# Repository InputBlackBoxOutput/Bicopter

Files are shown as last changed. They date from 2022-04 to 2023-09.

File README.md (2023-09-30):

# Bicopter
A bicopter is a type of unmanned aerial vehicle that features two rotors for generating lift and controlling its movement. Unlike traditional quadcopters, which have four rotors, bicopters use only two rotors to achieve flight.

## Assembly
- Uses a PCB that acts at the frame and provides support to all the other components.
- Two motors each connected to a servo motor using a 3D-printed contraption
- The propellers have a mounting boss with a hole diameter equal to the motor shaft diameter
- The servos are attached to the PCB using strong glue 
- The rechargeable lithium-ion (Li-ion) battery is mounted under the PCB using zip ties
- The landing gears are 3D printed and attached to the PCB using screws and nuts

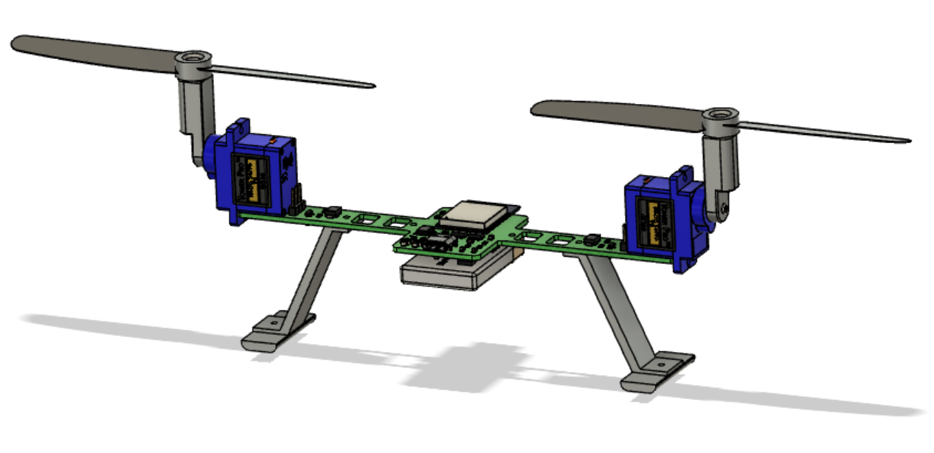
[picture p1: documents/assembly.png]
assembly


## Hardware block diagram
- ESP32 WROOM: 
	- Control BLDC and servo motors to maintain flight
	- Communicate with the remote controller
- BLDC motor: Provide lift
- Servo motor: Tilt BLDC motors to move the craft
- LED: 
	- Help locate the craft in the dark
	- Indicate battery voltage level 
- LiPo battery + BMS: 
	- Charge the battery 
	- Check battery voltage level
	- Perform power conversion
 
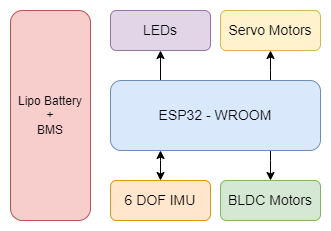
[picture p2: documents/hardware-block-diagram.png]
Hardware block diagram


## Application Interface Screenshot
- Connect to the bicopter
- Send flight control information
- Receive and display battery and communication strength information

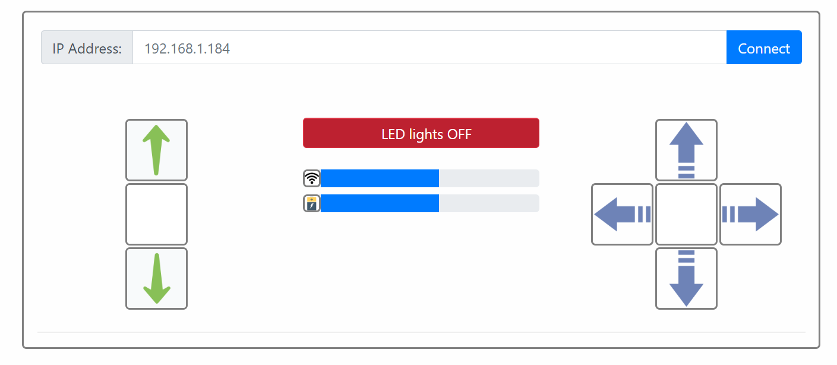
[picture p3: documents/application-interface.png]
Application interface


### Made with lots of ⏱️, 📚 and ☕ by InputBlackBoxOutput

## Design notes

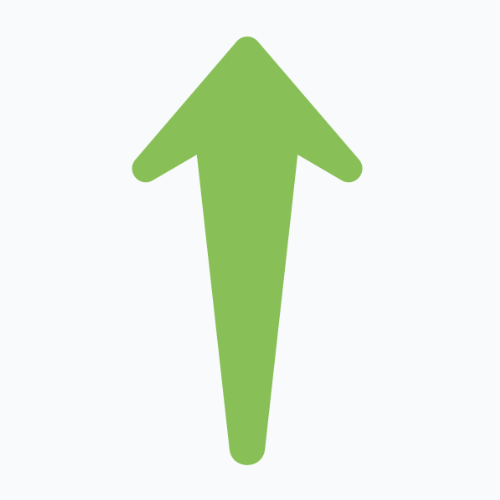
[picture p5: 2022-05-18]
application/render/img/arrow-up.png

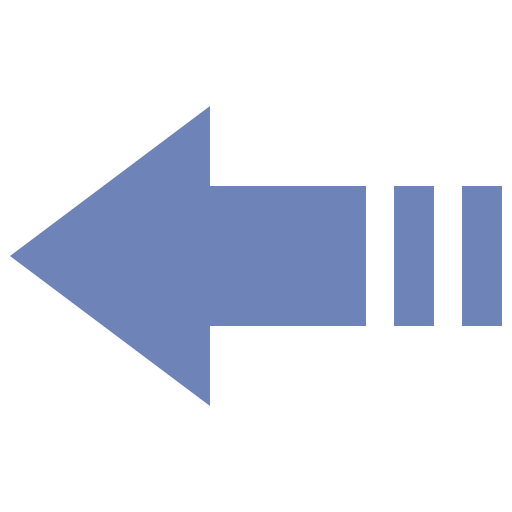
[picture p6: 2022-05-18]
application/render/img/arrow-left.png

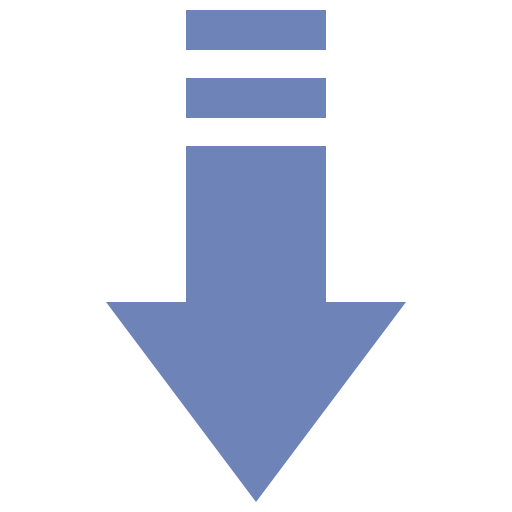
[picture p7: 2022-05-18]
application/render/img/arrow-backward.png

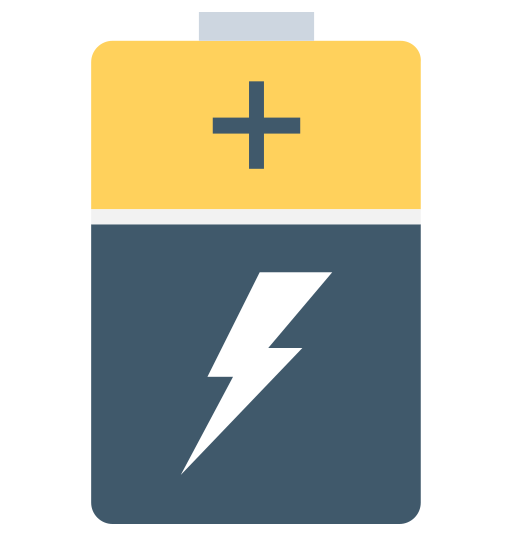
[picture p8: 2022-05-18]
application/render/img/battery.png

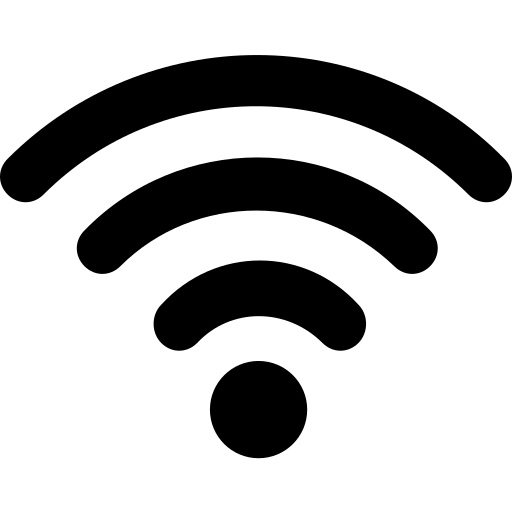
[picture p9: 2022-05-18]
application/render/img/connected.png

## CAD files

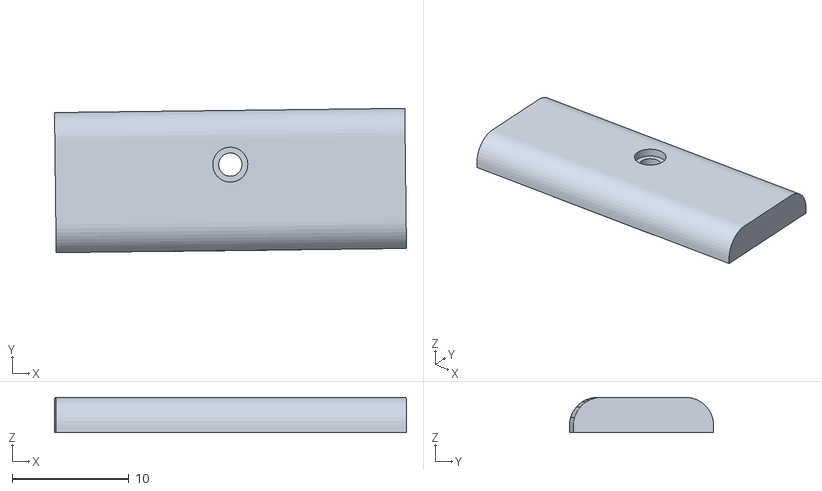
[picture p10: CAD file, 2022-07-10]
3D printed parts/landing-gear-skid.stl
30.1 x 12.4 x 3.02

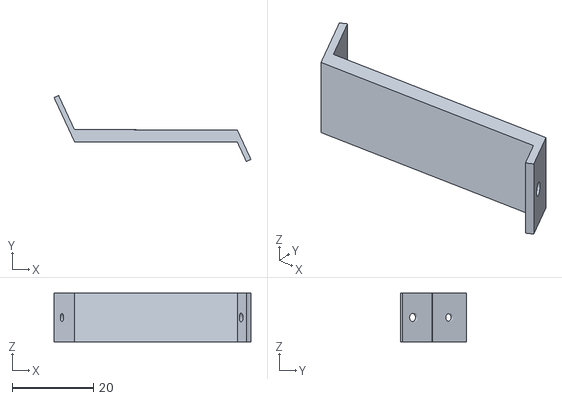
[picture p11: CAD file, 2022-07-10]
3D printed parts/landing-gear-leg.stl
48.4 x 16.3 x 12.0

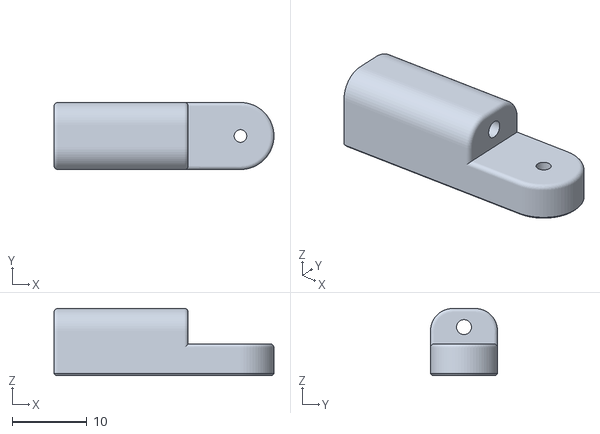
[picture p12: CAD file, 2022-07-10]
3D printed parts/motor-holder.stl
29.5 x 9.00 x 9.00

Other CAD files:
3D printed parts/landing-gear-leg.f3d
3D printed parts/landing-gear-skid.f3d
3D printed parts/motor-holder.f3d

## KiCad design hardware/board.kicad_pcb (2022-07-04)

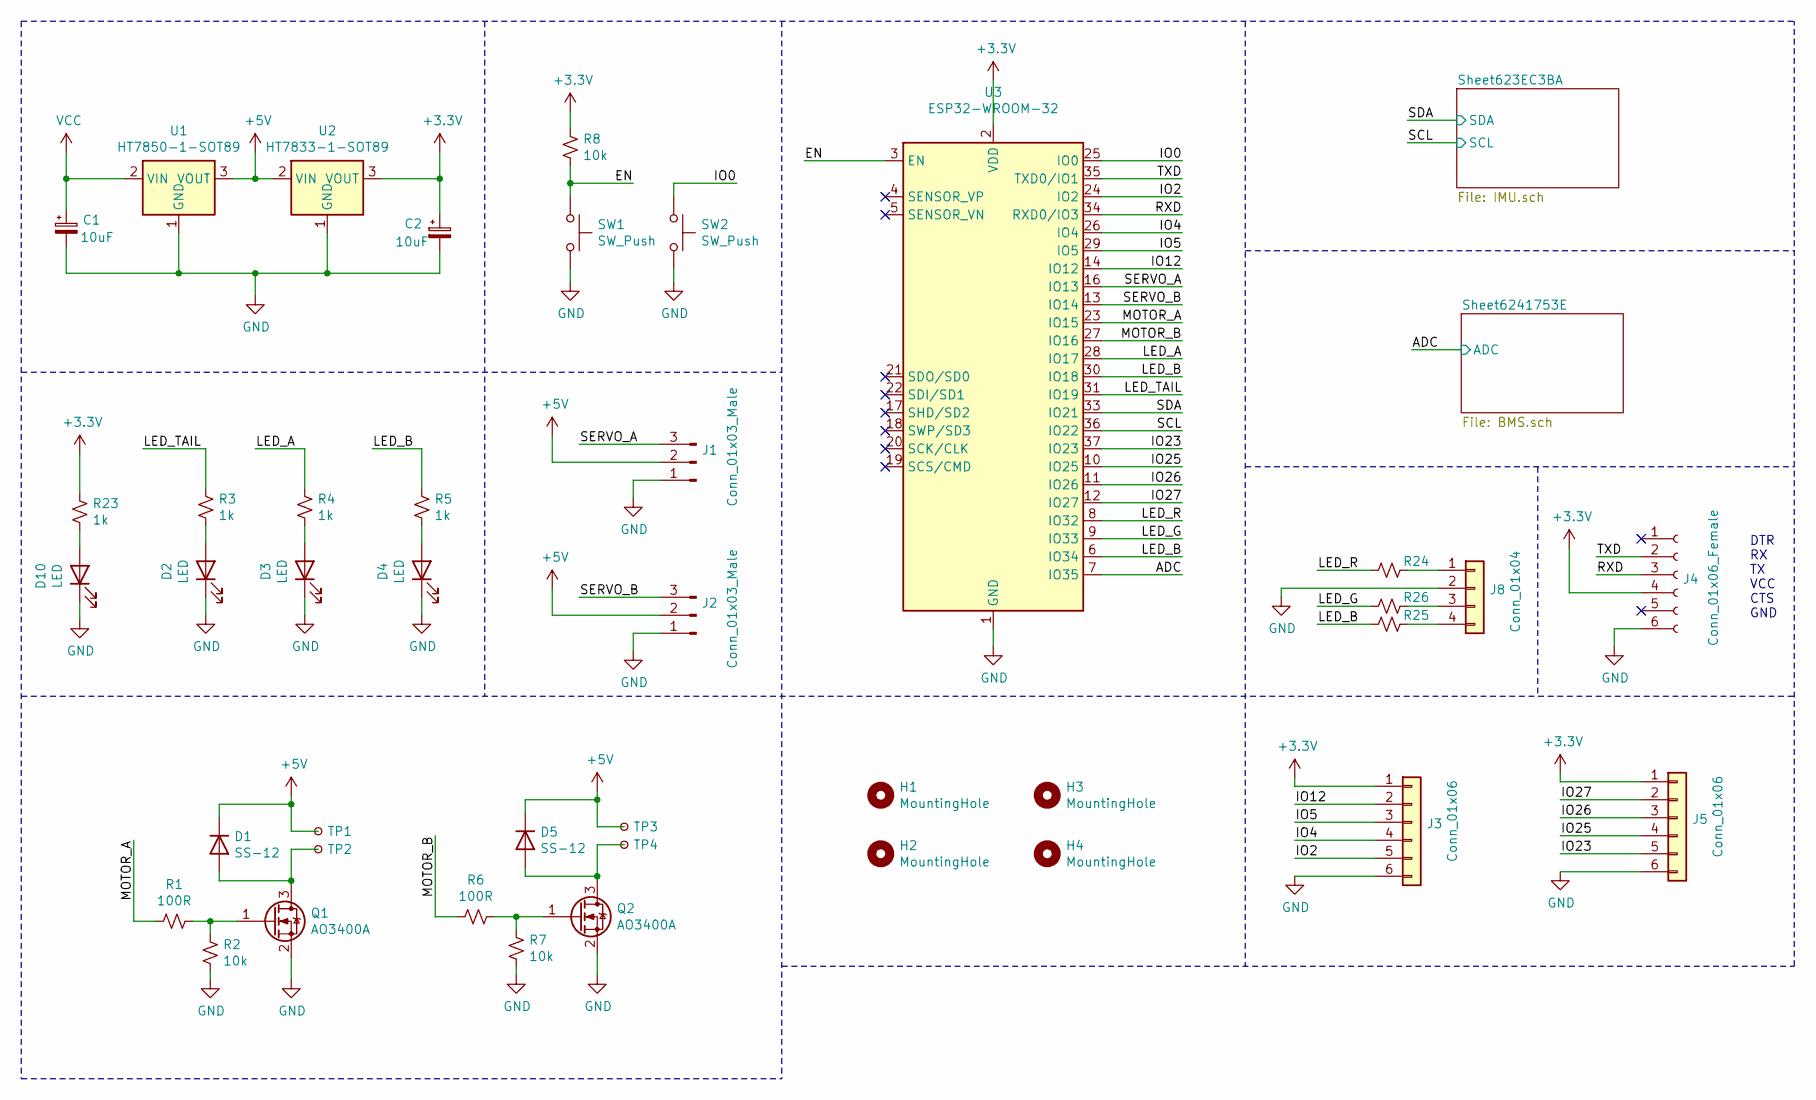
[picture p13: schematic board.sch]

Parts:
C1, C2: 10uF; C_0805_2012Metric_Pad1.18x1.45mm_HandSolder
D1, D5: SS-12; D_SMB
D2, D3, D4, D10: LED; LED_0805_2012Metric_Pad1.15x1.40mm_HandSolder
H1, H2, H3, H4: MountingHole; MountingHole_2.2mm_M2
J1, J2: Conn_01x03_Male; PinHeader_1x03_P2.54mm_Vertical
J3, J5: Conn_01x06; PinHeader_1x06_P1.00mm_Vertical_SMD_Pin1Left
J4: Conn_01x06_Female; Wire-Pad-01x06
J8: Conn_01x04; Wire-Pad-01x04
Q1, Q2: AO3400A; SOT-23
R1, R6, R24: 100R; R_0805_2012Metric_Pad1.20x1.40mm_HandSolder
R2, R7, R8: 10k; R_0805_2012Metric_Pad1.20x1.40mm_HandSolder
R3, R4, R5, R23, R25, R26: 1k; R_0805_2012Metric_Pad1.20x1.40mm_HandSolder
SW1, SW2: SW_Push; SW_SPST_B3U-1000P
TP1: A+; Wire-Pad
TP2: A-; Wire-Pad
TP3: B+; Wire-Pad
TP4: B-; Wire-Pad
U1: HT7850-1-SOT89; SOT-89-3
U2: HT7833-1-SOT89; SOT-89-3
U3: ESP32-WROOM-32

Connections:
+3V3: C2.1, J3.1, J4.4, J5.1, R8.1, R23.1, U2.3 (VOUT), U3.2 (VDD); also elsewhere on the board
+5V: D1.1 (K), D5.1 (K), J1.2, J2.2, TP1.1, TP3.1, U1.3 (VOUT), U2.2 (VIN)
/ADC: U3.7 (IO35); also elsewhere on the board
/EN: R8.2, SW1.1, U3.3 (EN)
/IO0: SW2.1, U3.25 (IO0)
/IO2: J3.5, U3.24 (IO2)
/IO4: J3.4, U3.26 (IO4)
/IO5: J3.3, U3.29 (IO5)
/IO12: J3.2, U3.14 (IO12)
/IO23: J5.5, U3.37 (IO23)
/IO25: J5.4, U3.10 (IO25)
/IO26: J5.3, U3.11 (IO26)
/IO27: J5.2, U3.12 (IO27)
/LED_A: R4.1, U3.28 (IO17)
/LED_B: R5.1, R25.2, U3.6 (IO34), U3.30 (IO18)
/LED_G: R26.2, U3.9 (IO33)
/LED_R: R24.2, U3.8 (IO32)
/LED_TAIL: R3.1, U3.31 (IO19)
/MOTOR_A: R1.2, U3.23 (IO15)
/MOTOR_B: R6.2, U3.27 (IO16)
/RXD: J4.3, U3.34 (RXD0/IO3)
/SCL: U3.36 (IO22); also elsewhere on the board
/SDA: U3.33 (IO21); also elsewhere on the board
/SERVO_A: J1.3, U3.16 (IO13)
/SERVO_B: J2.3, U3.13 (IO14)
/TXD: J4.2, U3.35 (TXD0/IO1)
GND: C1.2, C2.2, D2.1 (K), D3.1 (K), D4.1 (K), D10.1 (K), J1.1, J2.1, J3.6, J4.6, J5.6, J8.2, Q1.2 (S), Q2.2 (S), R2.2, R7.2, SW1.2, SW2.2, U1.1 (GND), U2.1 (GND), U3.1 (GND), U3.15 (GND), U3.38 (GND), U3.39 (GND); also elsewhere on the board
unnamed: D1.2 (A), Q1.3 (D), TP2.1
unnamed: D2.2 (A), R3.2
unnamed: D3.2 (A), R4.2
unnamed: D4.2 (A), R5.2
unnamed: D5.2 (A), Q2.3 (D), TP4.1
unnamed: D10.2 (A), R23.2
unnamed: J8.1, R24.1
unnamed: J8.3, R26.1
unnamed: J8.4, R25.1
unnamed: Q1.1 (G), R1.1, R2.1
unnamed: Q2.1 (G), R6.1, R7.1
VCC: C1.1, U1.2 (VIN); also elsewhere on the board

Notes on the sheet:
DTR RX TX VCC CTS GND

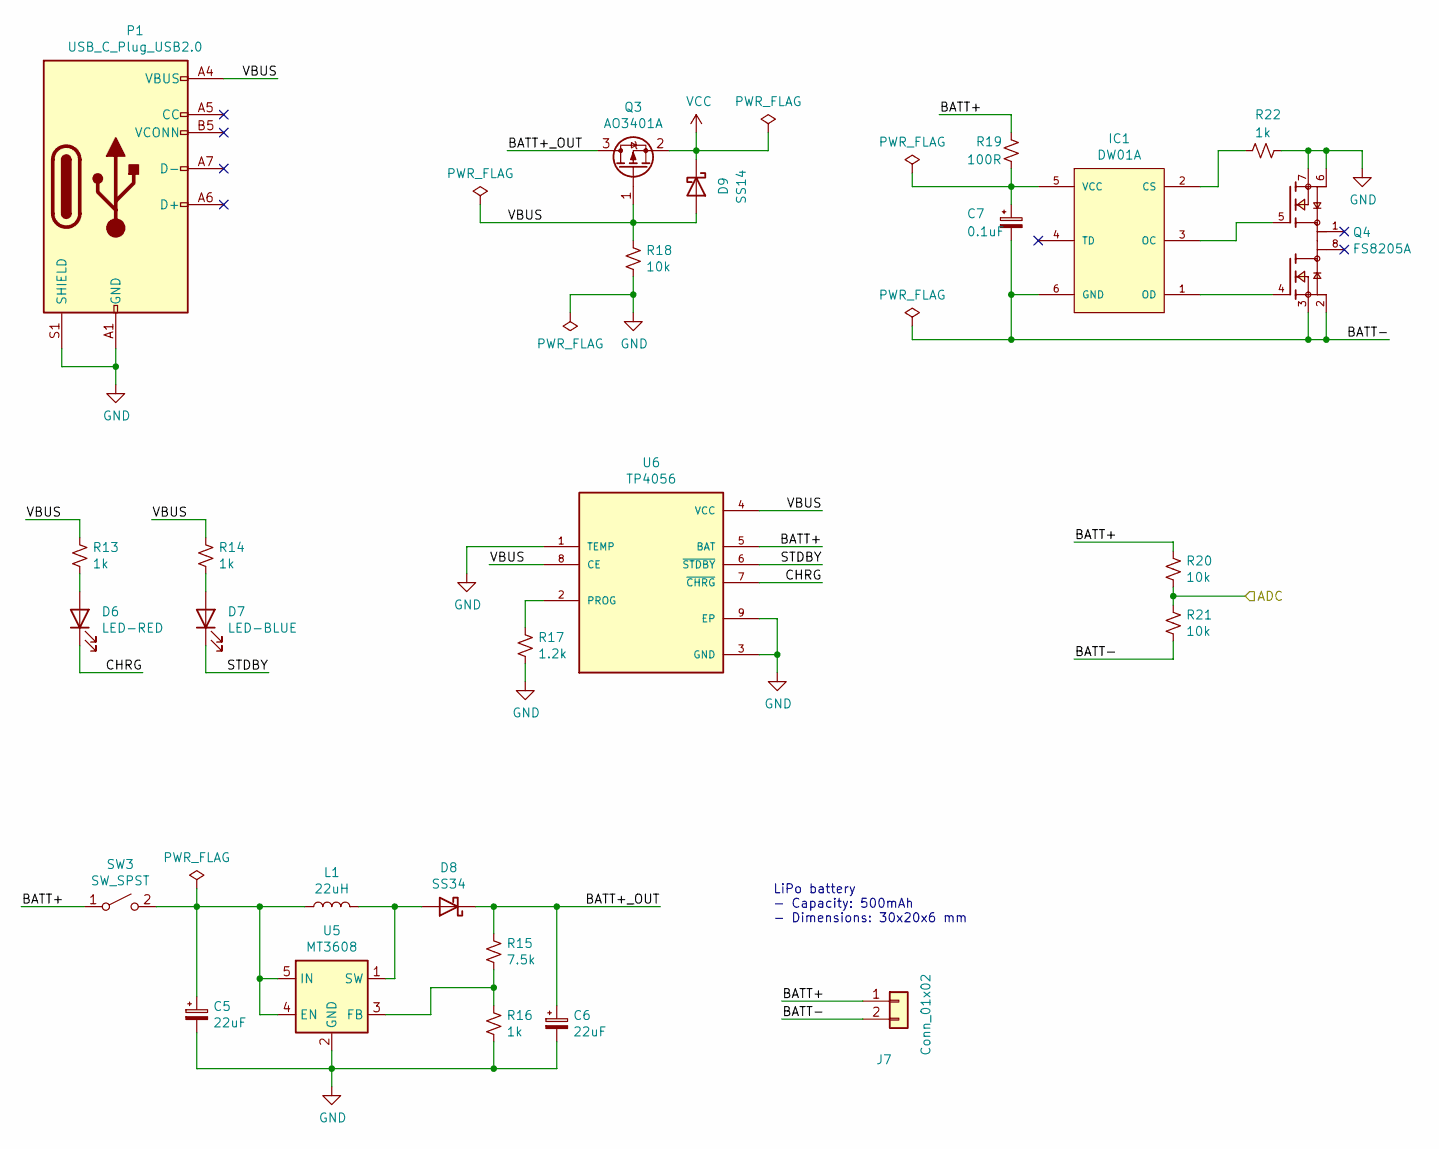
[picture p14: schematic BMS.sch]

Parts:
C5, C6: 22uF; C_0805_2012Metric_Pad1.18x1.45mm_HandSolder
C7: 0.1uF; C_0805_2012Metric_Pad1.18x1.45mm_HandSolder
D6: LED-RED; LED_0805_2012Metric_Pad1.15x1.40mm_HandSolder
D7: LED-BLUE; LED_0805_2012Metric_Pad1.15x1.40mm_HandSolder
D8: SS34; D_SMC_Handsoldering
D9: SS14; D_SMB
IC1: DW01A; SOT-23-6_Handsoldering; MPN DW01A; LCSC C351410
J7: Conn_01x02; Wire-Pad-01x02
L1: 22uH; L_10.4x10.4_H4.8
P1: USB_C_Plug_USB2.0; USB_C_Receptacle_HRO_TYPE-C-31-M-12
Q3: AO3401A; SOT-23
Q4: FS8205A; SOP65P640X120-8N; PARTREV 1.7
R13, R14, R16, R22: 1k; R_0805_2012Metric_Pad1.20x1.40mm_HandSolder
R15: 7.5k; R_0805_2012Metric_Pad1.20x1.40mm_HandSolder
R17: 1.2k; R_0805_2012Metric_Pad1.20x1.40mm_HandSolder
R18, R20, R21: 10k; R_0805_2012Metric_Pad1.20x1.40mm_HandSolder
R19: 100R; R_0805_2012Metric_Pad1.20x1.40mm_HandSolder
SW3: SW_SPST; SW_SPDT_PCM12
U5: MT3608; SOT-23-6
U6: TP4056; SOP127P600X175-9N

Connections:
/ADC: R20.2, R21.1; also elsewhere on the board
/Sheet6241753E/BATT+: J7.1, R19.1, R20.1, SW3.1 (A), U6.5 (BAT)
/Sheet6241753E/BATT+_OUT: C6.1, D8.1 (K), Q3.3 (D), R15.1
/Sheet6241753E/BATT-: C7.2, IC1.6 (GND), J7.2, Q4.2, Q4.3, R21.2
/Sheet6241753E/CHRG: D6.1 (K), U6.7 (~CHRG)
/Sheet6241753E/STDBY: D7.1 (K), U6.6 (~STDBY)
/Sheet6241753E/VBUS: D9.2 (A), P1.A4 (VBUS), P1.A9 (VBUS), P1.B4 (VBUS), P1.B9 (VBUS), Q3.1 (G), R13.1, R14.1, R18.1, U6.4 (VCC), U6.8 (CE)
GND: C5.2, C6.2, P1.A1 (GND), P1.A12 (GND), P1.B1 (GND), P1.B12 (GND), P1.S1 (SHIELD), Q4.6, Q4.7, R16.2, R17.2, R18.2, R22.1, U5.2 (GND), U6.1 (TEMP), U6.3 (GND), U6.9 (EP); also elsewhere on the board
unnamed: C5.1, L1.1, SW3.2 (B), U5.4 (EN), U5.5 (IN)
unnamed: C7.1, IC1.5 (VCC), R19.2
unnamed: D6.2 (A), R13.2
unnamed: D7.2 (A), R14.2
unnamed: D8.2 (A), L1.2, U5.1 (SW)
unnamed: IC1.1 (OD), Q4.4
unnamed: IC1.2 (CS), R22.2
unnamed: IC1.3 (OC), Q4.5
unnamed: R15.2, R16.1, U5.3 (FB)
unnamed: R17.1, U6.2 (PROG)
VCC: D9.1 (K), Q3.2 (S); also elsewhere on the board

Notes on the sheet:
LiPo battery - Capacity: 500mAh - Dimensions: 30x20x6 mm

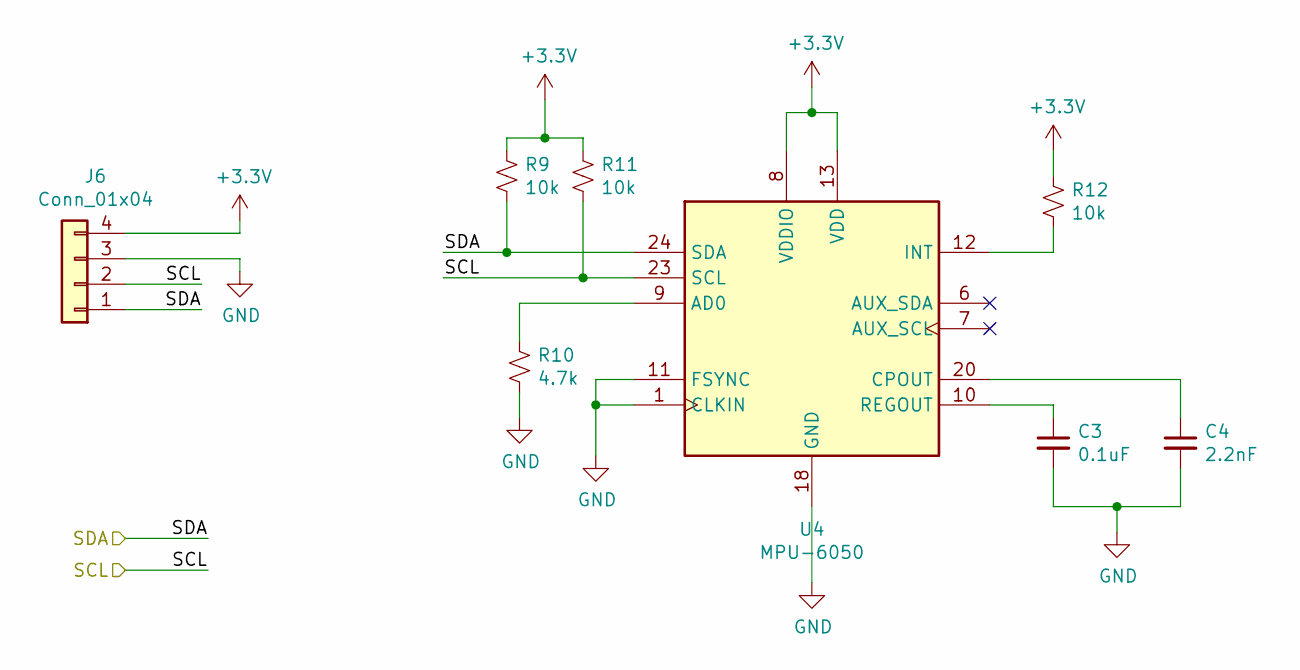
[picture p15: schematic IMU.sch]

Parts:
C3: 0.1uF; C_0805_2012Metric_Pad1.18x1.45mm_HandSolder
C4: 2.2nF; C_0805_2012Metric_Pad1.18x1.45mm_HandSolder
J6: Conn_01x04; Wire-Pad-01x04
R9, R11, R12: 10k; R_0805_2012Metric_Pad1.20x1.40mm_HandSolder
R10: 4.7k; R_0805_2012Metric_Pad1.20x1.40mm_HandSolder
U4: MPU-6050; InvenSense_QFN-24_4x4mm_P0.5mm

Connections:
+3V3: J6.4, R9.1, R11.1, R12.1, U4.8 (VDDIO), U4.13 (VDD); also elsewhere on the board
/SCL: J6.2, R11.2, U4.23 (SCL); also elsewhere on the board
/SDA: J6.1, R9.2, U4.24 (SDA); also elsewhere on the board
GND: C3.2, C4.2, J6.3, R10.2, U4.1 (CLKIN), U4.11 (FSYNC), U4.18 (GND); also elsewhere on the board
unnamed: C3.1, U4.10 (REGOUT)
unnamed: C4.1, U4.20 (CPOUT)
unnamed: R10.1, U4.9 (AD0)
unnamed: R12.2, U4.12 (INT)

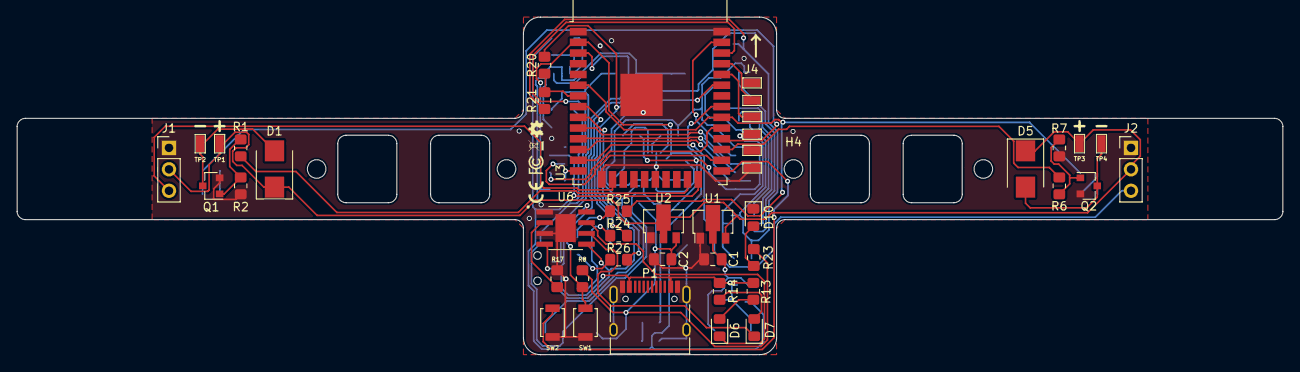
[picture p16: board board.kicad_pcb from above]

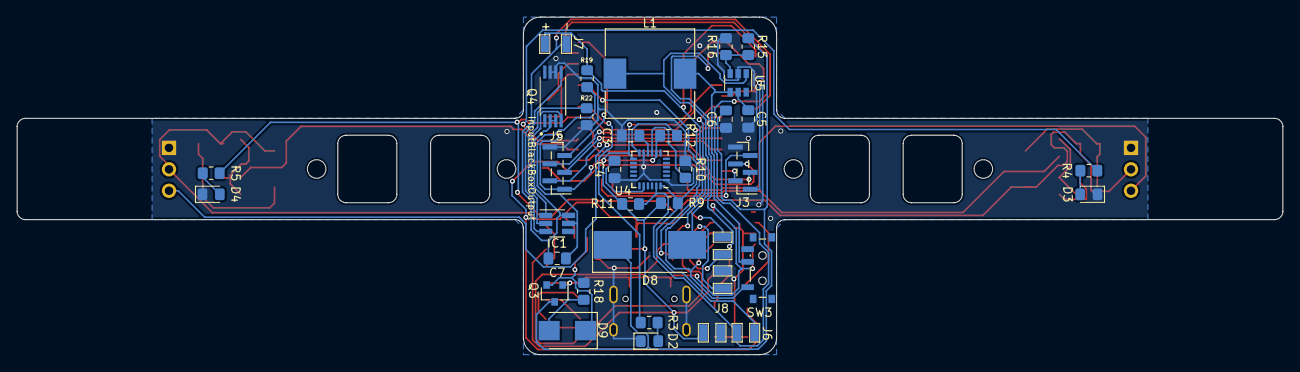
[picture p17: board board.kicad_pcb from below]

Board: 2 copper layers, 150.0 x 40.0 mm, 75 parts (34 on the bottom side), 59 nets.

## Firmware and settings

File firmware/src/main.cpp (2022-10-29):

#include <Arduino.h>

#include "servo.h"
#include "motor.h"
#include "LED.h"
#include "IMU.h"
#include "BMS.h"
#include "state.h"
#include "server.h"
#include "PID.h"

InertialMeasurementUnit imu;
TiltServo servoA(SERVO_A_PIN);
TiltServo servoB(SERVO_B_PIN);
Motor motorA(MOTOR_A_PIN);
Motor motorB(MOTOR_B_PIN);
LED led;
BMS bms;

ESP32Server server;
PIDController pid;
ControlState currentState;

#define LOOP_DELAY 300 // ms
unsigned long loopStartTime;
unsigned long elapsedTime;

void setup()
{
  Serial.begin(115200);

  pid.setup();
  server.setup();

  led.blinkLED(led.LED_TAIL, 2);
  loopStartTime = millis();
}

void loop()
{
  server.handleClient();

  // Update servo angles
  servoA.setServoAngle(currentState.servoAngle_A);
  servoA.setServoAngle(currentState.servoAngle_B);

  // Update motor PWM
  motorA.setDutyCyclePWM(currentState.motorPWM_A);
  motorB.setDutyCyclePWM(currentState.motorPWM_B);

  // Turn LEDs ON or OFF
  if (currentState.LED)
  {
    led.turnLEDOn(led.LED_A);
    led.turnLEDOn(led.LED_B);
    led.turnLEDOn(led.LED_TAIL);
  }
  else
  {
    led.turnLEDOff(led.LED_A);
    led.turnLEDOff(led.LED_B);
    led.turnLEDOff(led.LED_TAIL);
  }

  // Read battery voltage and blink tail LED if battery voltage is low
  currentState.batteryVoltage = bms.readBatteryVoltage();
  if (bms.isBatteryVoltageLow())
    led.blinkLED(led.LED_TAIL, 3);

  delay(LOOP_DELAY);

  // Sense tilt and update servo angles to maintain stability using PID
  elapsedTime = millis() - loopStartTime;
  imu.calculateTiltAngles(elapsedTime);
  loopStartTime = millis();

  pid.update();
}

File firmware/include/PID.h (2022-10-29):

#ifndef PID_H
#define PID_H

#include <Arduino.h>
#include <PID_v1.h>
#include "state.h"
#include "IMU.h"

extern ControlState currentState;
extern InertialMeasurementUnit imu;

#define KP_PITCH 0.25
#define KI_PITCH 0.5
#define KD_PITCH 0.5

#define KP_YAW 0.25
#define KI_YAW 0.5
#define KD_YAW 0.5

class PIDController
{
public:
    PIDController()
    {
        PID pitchControl(&sensePitchPID, &controlPitchPID, &setpoint, KP_PITCH, KI_PITCH, KD_PITCH, DIRECT);
        PID yawControl(&senseYawPID, &controlYawPID, &setpoint, KP_YAW, KI_YAW, KD_YAW, DIRECT);

        pid[0] = &pitchControl;
        pid[1] = &yawControl;
    }

    void setup();
    void update();

private:
    PID *pid[2];
    double sensePitchPID = 90;
    double senseYawPID = 90;
    double controlPitchPID = 90;
    double controlYawPID = 90;

    double setpoint = 90;
};

#endif // PID_H

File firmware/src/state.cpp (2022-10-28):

#include "state.h"

void ControlState::initControlState()
{
    motorPWM_A = 0;
    motorPWM_B = 0;
    servoAngle_A = 0;
    servoAngle_B = 0;
    
    LED = false;
    batteryVoltage = 4.20;
}

void ControlState::printControlState()
{
    Serial.print("Motor A PWM: ");
    Serial.println(motorPWM_A);
    Serial.print("Motor B PWM: ");
    Serial.println(motorPWM_B);

    Serial.print("Servo A angle: ");
    Serial.println(servoAngle_A);
    Serial.print("Servo B angle: ");
    Serial.println(servoAngle_B);

    Serial.print("LED: ");
    Serial.println(LED);

    Serial.print("Battery voltage: ");
    Serial.println(batteryVoltage);
}

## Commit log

2022-03-19 Schematics added
    [BMS.sch, IMU.sch, board.kicad_pcb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]
2022-03-19 PCB layout
    [BMS.sch, IMU.sch, board.sch]
2022-03-20 PCB routed
    [BMS.sch, board.dsn, board.kicad_pcb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]
2022-04-18 PCB: Mounting holes for landing gear
    [board.kicad_pcb, board.sch]
2022-05-02 Models of 3D printed parts added
    [landing-gear-leg.f3d, landing-gear-skid.f3d, motor-holder.f3d]
2022-05-02 PCB: Holes for LiPo battery zip tie added
    [board.kicad_pcb, board.sch]
2022-05-05 PCB: CE, FCC, WEEE and OSHW markings added
    [board.kicad_pcb]
2022-05-05 PCB: Fixed connection to ground plane
    [board.kicad_pcb]
2022-05-07 Firmware: LED
2022-05-07 Firmware: Servo motor + BLDC motor
2022-05-10 Firmware: IMU
2022-05-25 Electron application: Button controls
2022-06-20 Electron application: Adapt to small screen devices
2022-07-04 Folder reorganized: hardware
    [board.kicad_pcb, board.sch]
2022-07-04 PCB: Minor changes
    [board.kicad_pcb, board.sch]
2022-07-10 3D printed parts: STL files
    [landing-gear-leg.stl, landing-gear-skid.stl, motor-holder.stl]
2022-10-13 Firmware: BMS
2022-10-29 Firmware: PID
2022-10-29 Application: WiFi strength + Battery voltage stats
